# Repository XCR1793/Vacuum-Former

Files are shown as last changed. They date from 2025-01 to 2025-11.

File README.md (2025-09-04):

# Vacuum Former
An affordable vacuum former capable of forming medium to large bucks and molds. The system must also be safe for anyone to use in both hardware and electronics (as this requires mains).

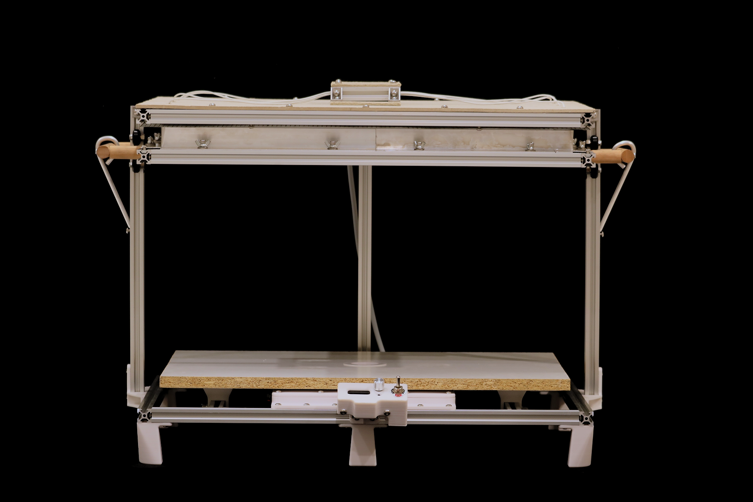
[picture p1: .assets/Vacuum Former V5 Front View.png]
Project_Image


## Features
* Hybrid Frame - Rigid aluminium combined with cheap cement fiber boards results in a fireproof frame.
* RCBO - Short, fault and overcurrent protection.
* SSR - PWM based temperature control.

## [Hardware](/Hardware/README.md)
The frame is designed to be collapsible so it is easily stored. The heater box, material frame and base plattern uses the same 440mm x 640mm aluminium 2020 frames which makes it easy to
fabricate and assemble. All components that get close to the heatsource is fireproof and areas that are not subject to heat are 3D printed to both save cost and time to construct.

## [Embedded](/Embedded/README.md)
Although dangerous, many safety features were implemented to reduce the risk of injury. This includes breakers and rcbos to detect shorts, faults and if the user accidentally touches the
live wires. All electronics are rated to and beyond what is required to run the system of 240VAC at 20A, this does mean however, that the user must have a port which can supply 15A and
beyond if you want to run the heater box. The average house hold outlet should provide 10A at 240VAC, however if your in the Americas you'll use 110VAC. This means in both senarios,
you will have to find a high current compatible port or else you will trip a breaker. If you dont have one, then you must remove 2 of the heating elements as each of them uses 1KW. This 
will however reduce the total amount of heat you can provided and may not be able to rais the temperature enough to heat difficult to form materials such as polycarbonate which requires 
around 240C to form properly.

## Roadmap
* Milestones: Hardware Assembly Complete
* Milestones: Electrical Wiring
* Milestones: Electrical Box
* Milestones: Controller Box
* Work In Progress: Datasheet
* Planned: Assembly Instructions

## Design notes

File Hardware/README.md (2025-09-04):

# Hardware

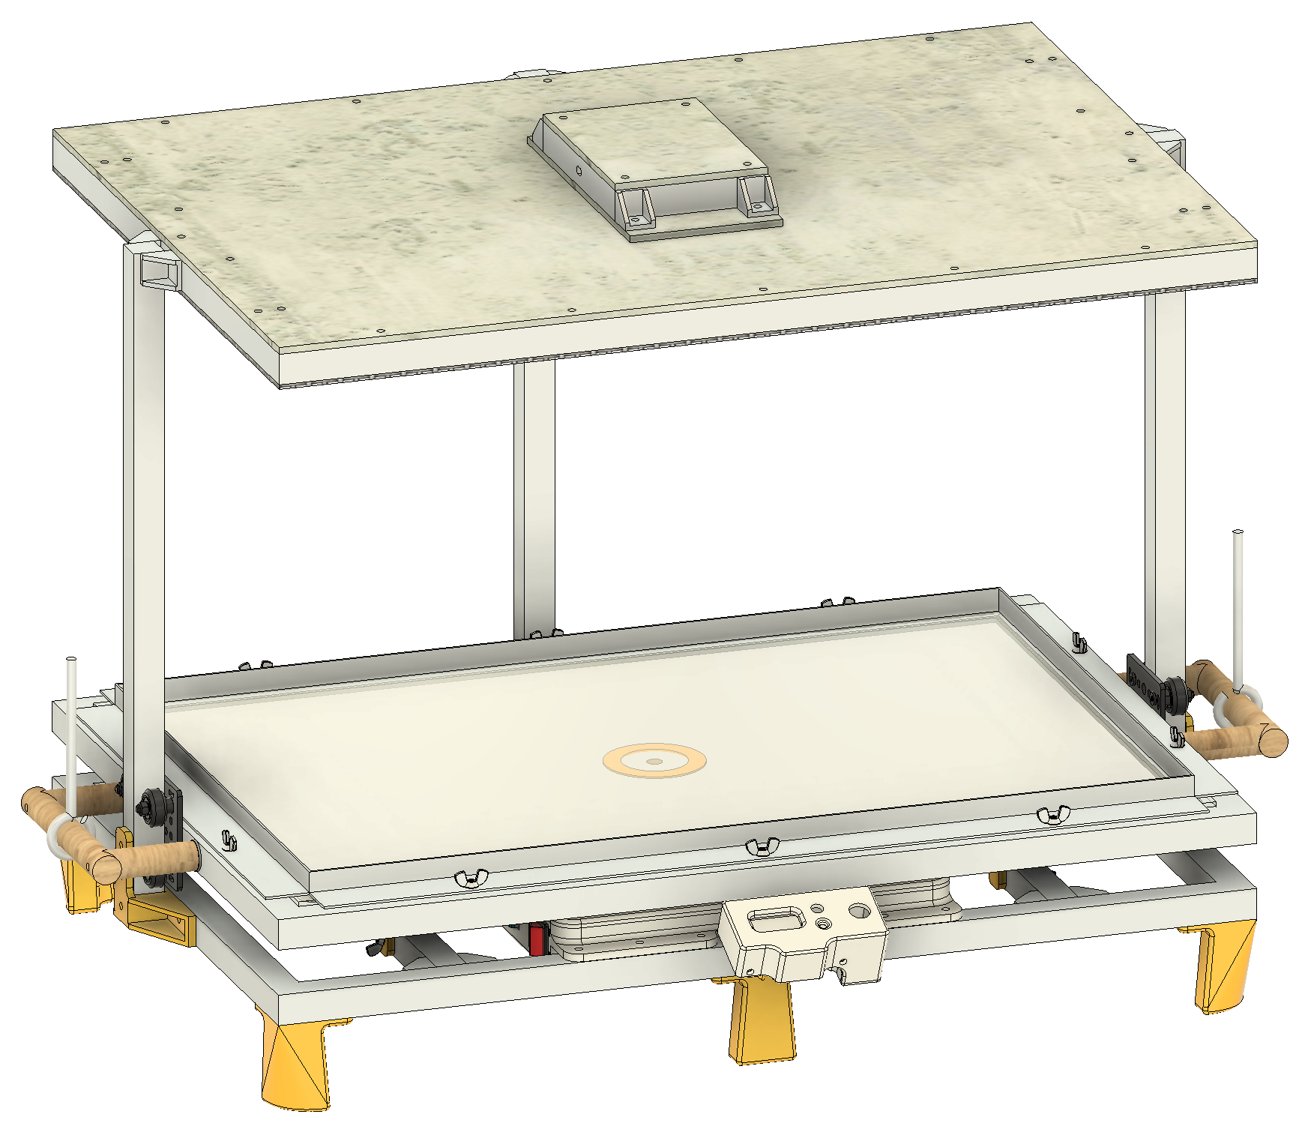
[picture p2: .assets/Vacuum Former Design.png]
Hardware_Capabilities


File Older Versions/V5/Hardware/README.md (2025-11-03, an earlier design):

# Hardware

Hardware_Capabilities

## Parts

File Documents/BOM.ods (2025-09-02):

Heater
Components | Size (mm) | Quantity
Aluminium Extrusion (2020) | 440 | 2
Aluminium Extrusion (2020) | 600 | 2
Aluminium Right Angle | 20 x 20 x 460 | 2
Metal Mesh | 440 x 640 | 1
Cement Fibre Board | 440 x 640 | 3
M5 Bolt | 10 | 18
M5 Bolt | 20 | 16
M5 T Nut | N/A | 30
Carbon Fibre Quartz Heater | 520 x 12 | 4
M5 Washer | N/A | 16
Material Frame
Components | Size (mm) | Quantity
Aluminium Extrusion (2020) | 440 | 2
Aluminium Extrusion (2020) | 600 | 2
Aluminium Right Angle | 30 x 15 x 958 | 2
Aluminium Right Angle | 20 x 12 x 1000 | 2
M5 Fly Nut | N/A | 10
M5 Bolt | 10 | 14
M5 Bolt (Fly Nut Male Adaptor) | 10 | 10
Platen
Components | Size (mm) | Quantity
Aluminium Extrusion (2020) | 440 | 2
Aluminium Extrusion (2020) | 600 | 2
Aluminium Extrusion (2020) | 400 | 2
Corner Bracket | N/A | 4
M5 Fly Nut | N/A | 4
M5 T Nut | N/A | 22
M5 Bolt | 10 | 12
Overall
Components | Size (mm) | Quantity
Aluminium Extrusion (2020) | 440 | 3
Aluminium 2020 Gantry Slider | N/A | 2
Corner Bracket | N/A | 6
Wooden Dowel (19mm OD) | 259 | 2
M5 Bolt | 75 | 4
M5 Washer | N/A | 4
M10 Washer | N/A | 4
M5 Bolt | 10 | 39
M5 T Nut | N/A | 43
Aluminium Rod (6.3mm OD) | 200 | 2
Electronics
Components | Size (mm) | Quantity
IEC C20 Port (Mains In) | N/A | 1
Anderson Port (Emergency Stop Port) | N/A | 1
IEC C19 Port (Heater Out) | N/A | 1
IEC C20 to Cables (Heater Adapter) | N/A | 1
Anderson to Cables (PWR Adapter) | N/A | 1
IEC C16 (Vacuum Pump Port) | N/A | 1
5V 2A PSU | 39 x 30 x 70 | 1
SSR (Heater, DC Controlled) | N/A | 1
SSR (Pump, DC Controlled) | N/A | 1
RCBO (20A) | N/A | 1
PWM Pulse Generator | N/A | 1
DPDT Switch (ON-Off-ON) | N/A | 1
Power Switch | N/A | 1
TOTAL Cost List |  | Total Cost: | $481.80 | AUD
Components | Size (mm) | Quantity | Cost (Total) | Link
Aluminium Extrusion (2020) | 1500 | 6 | $160.52 | Makerstore (https://www.makerstore.com.au/product/v-slot-20-x-20mm/?attribute_pa_length=1500mm)
Aluminium Right Angle | 20 x 20 x 1000 | 1 | $10.05 | Bunnings (https://www.bunnings.com.au/metal-mate-20-x-20-x-1-5mm-1m-aluminium-equal-angle-silver-1m_p1067865)
Aluminium Right Angle | 20 x 12 x 1000 | 2 | $16.32 | Bunnings (https://www.bunnings.com.au/metal-mate-20-x-12-x-1-4mm-1m-aluminium-unequal-angle-silver_p1067823)
Aluminium Right Angle | 30 x 15 x 1000 | 2 | $22.10 | Bunnings (https://www.bunnings.com.au/metal-mate-30-x-30-x-1-5mm-1m-silver-aluminium-angle-silver-1m_p1130510)
M5 Bolt | 10 | 83 | $14.77 | Aliexpress (https://www.aliexpress.com/item/1005007661689652.html?)
M5 T Nut | N/A | 115 | $17.62 | Aliexpress (https://www.aliexpress.com/item/1005007383347166.html?)
M5 Bolt | 20 | 16 | $12.71 | Aliexpress (https://www.aliexpress.com/item/32894530938.html?)
M5 Bolt | 75 | 4 | $2.05 | Bunnings (https://www.bunnings.com.au/pinnacle-m5-x-75mm-zinc-plated-round-head-bolts-and-nuts-4-pack_p0247271)
Carbon Fibre Quartz Heater | 520 x 12 | 4 | $51.37 | Aliexpress (https://www.aliexpress.com/item/1005007168603613.html?)
Aluminium Rod (6.3mm OD) | 1000 | 1 | $3.17 | Bunnings (https://www.bunnings.com.au/metal-mate-6-3mm-x-1m-aluminium-solid-rod-6-3mm_p1130541)
M5 Fly Nut | N/A | 14 | $6.61 | Aliexpress (https://www.aliexpress.com/item/1005006072038223.html?)
M5 Bolt (Fly Nut Male Adaptor) | 14mm | 14 | $9.13 | Aliexpress (https://www.aliexpress.com/item/32810872544.html?)
Cement Fibre Board | 440 x 640 | 3 | $12.55 | Bunnings (https://www.bunnings.com.au/james-hardie-hardieflex-2400-x-450-x-4-5mm-eaves-1-08m-_p0714491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)
Aluminium 2020 Gantry Slider | N/A | 2 | $10.99 | Aliexpress (https://www.aliexpress.com/item/1005006683869048.html?)
Metal Mesh | 440 x 640 | 1 | $14.99 | Bunnings (https://www.bunnings.com.au/rapidmesh-600-x-900-x-0-6mm-6-5-x-6-5-silver-wire-mesh-panel_p0203641)
Corner Bracket | N/A | 10 | $7.03 | Aliexpress (https://www.aliexpress.com/item/1005008248112282.html?)
Wooden Dowel (19mm OD) | 518 | 1 | $11.50 | Bunnings (https://www.bunnings.com.au/porta-19-x-19mm-1-2m-clear-pine-dowel_p8493988)
M10 Washer | N/A | 4 | $1.12 | Bunnings (https://www.bunnings.com.au/zenith-m10-hot-dip-galvanised-flat-round-washers_p2442070)
M5 Washer | N/A | 20 | $2.47 | Aliexpress (https://www.aliexpress.com/item/4000174460068.html?)
IEC C20 & C19 | N/A | 1 | $9.86 | Aliexpress (https://www.aliexpress.com/item/10000045738141.html?)
IEC C20 to Cables | N/A | 1 | $7.98 | Aliexpress (https://www.aliexpress.com/item/1005006996912471.html?)
IEC C16 (Vacuum Pump Port) | N/A | 1 | $5.93 | Aliexpress (https://www.aliexpress.com/item/1005005914216268.html?)
5V 2A PSU | 39 x 30 x 70 | 1 | $7.69 | Aliexpress (https://www.aliexpress.com/item/1005005552969433.html?)
SSR (DC Controlled AC) | N/A | 2 | $15.26 | Aliexpress (https://www.aliexpress.com/item/1005005837105164.html?)
RCBO (20A) | N/A | 1 | $41.29 | Bunnings (https://www.bunnings.com.au/deta-residual-circuit-breaker-with-overload-protection-20ah_p0131971)
PWM Pulse Generator | N/A | 1 | $6.72 | Aliexpress (https://www.aliexpress.com/item/1005006717341304.html?)
DPDT Switch (ON-Off-ON) | N/A | 1 | $11.96 | Aliexpress (https://www.aliexpress.com/item/1005004411546037.html?)
Power Switch | N/A | 1 | $5.90 | Aliexpress (https://www.aliexpress.com/item/33041128258.html?)

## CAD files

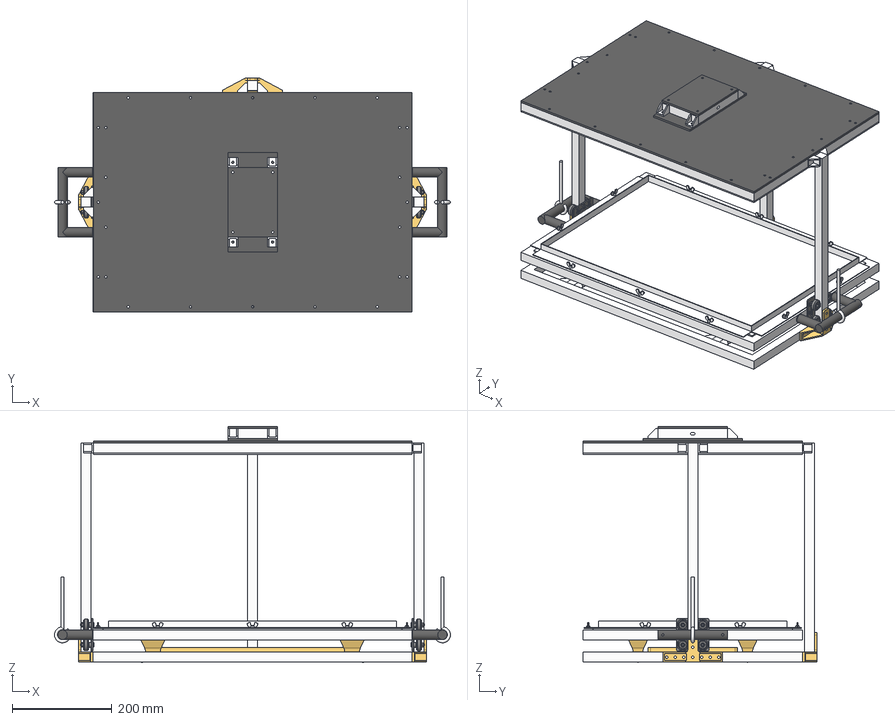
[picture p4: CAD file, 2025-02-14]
Hardware/Vacuum Former V5 Main.step
795.3 x 469.0 x 474.2 mm
V-Slot Gantry Plate 20mm x 2
Low Profile Screw M5 v1 x 8
Nylon Insert Lock Nut M5 x 8
Aluminum Spacer 6mm x 4
Eccentric Spacer 6mm v1 x 4
Ball Bearing 5 x 16 x 5 x 16
Precision Shim 8 x 5 x 1 x 8
Xtreme Solid V Wheel x 8
WING NUT M4 x 0.7mm Thread x 15
Carbon Fiber Quartz Heating Element (52cm) Ref x 4
Handles
Support Link R
Support Link L

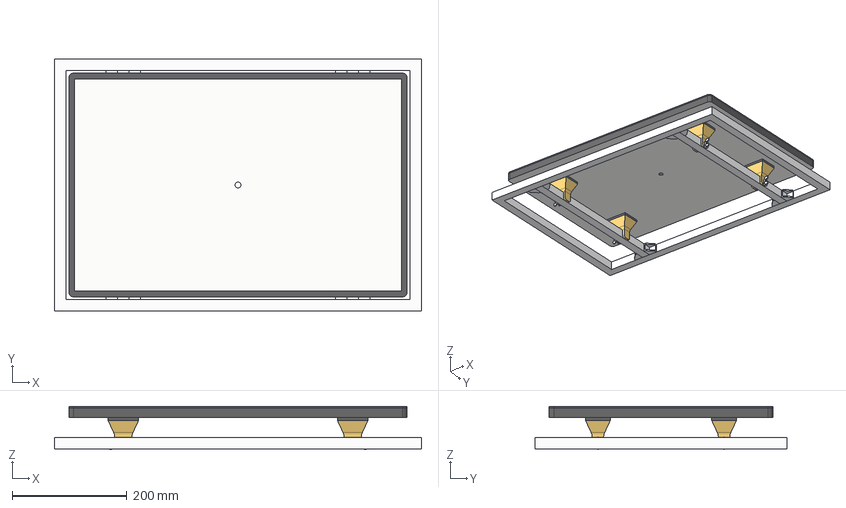
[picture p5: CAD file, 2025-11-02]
Hardware/Vacuum Former V5 Platen.step
640.0 x 440.0 x 75.2 mm
WING NUT M4 x 0.7mm Thread x 4

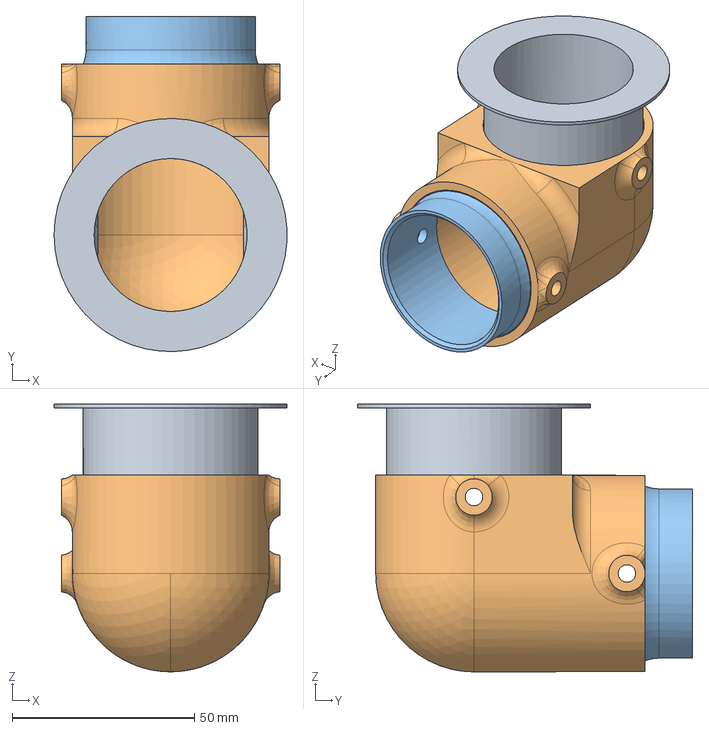
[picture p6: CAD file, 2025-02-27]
Hardware/Vacuum Former Platen Adapter V2.step
63.9 x 92.0 x 73.5 mm

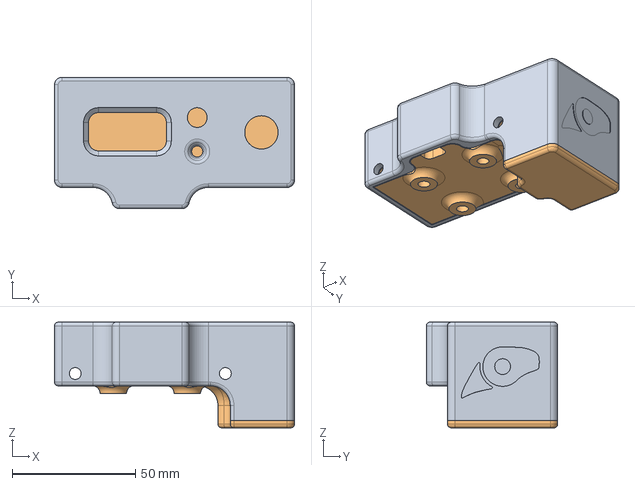
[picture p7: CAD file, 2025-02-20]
Hardware/Vacuum Former V5 Control Box.step
97.2 x 53.2 x 42.8 mm

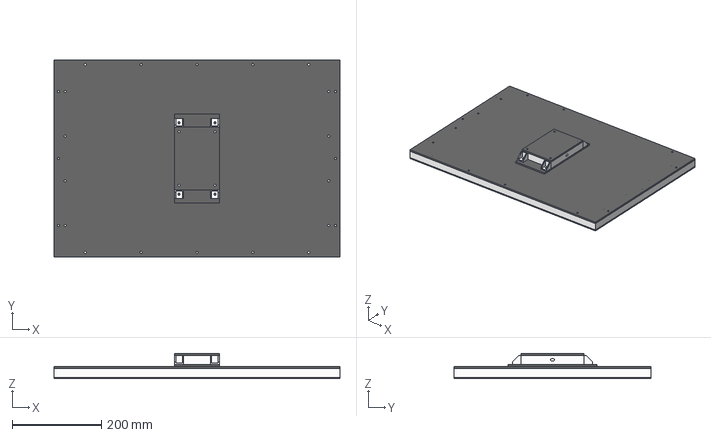
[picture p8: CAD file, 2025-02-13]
Hardware/Vacuum Former V5 Heater Box.step
640.0 x 440.0 x 56.5 mm
Carbon Fiber Quartz Heating Element (52cm) Ref x 4

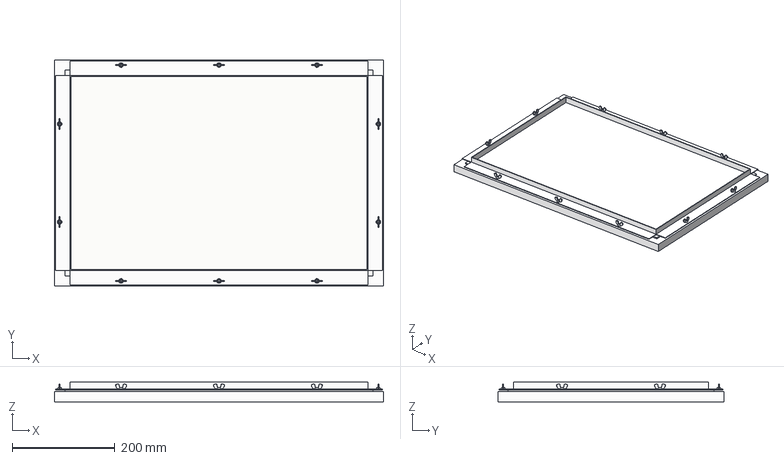
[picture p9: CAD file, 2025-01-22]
Hardware/Vacuum Former V5 Material Frame.step
640.0 x 440.0 x 38.0 mm
WING NUT M4 x 0.7mm Thread x 11

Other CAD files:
Hardware/Vacuum Former Platen Adapter V2.f3d
Hardware/Vacuum Former V5 Control Box.f3d
Hardware/Vacuum Former V5 Electrical Box.f3z
Hardware/Vacuum Former V5 Heater Box.f3z
Hardware/Vacuum Former V5 Main.f3z
Hardware/Vacuum Former V5 Material Frame.f3z
Hardware/Vacuum Former V5 Platen.f3z
Older Versions/V5/Hardware/Vacuum Former Platen Adapter V2.f3d
Older Versions/V5/Hardware/Vacuum Former V5 Control Box.f3d
Older Versions/V5/Hardware/Vacuum Former V5 Electrical Box.f3z
Older Versions/V5/Hardware/Vacuum Former V5 Heater Box.f3z
Older Versions/V5/Hardware/Vacuum Former V5 Main.f3z
Older Versions/V5/Hardware/Vacuum Former V5 Material Frame.f3z
Older Versions/V5/Hardware/Vacuum Former V5 Platen.f3z

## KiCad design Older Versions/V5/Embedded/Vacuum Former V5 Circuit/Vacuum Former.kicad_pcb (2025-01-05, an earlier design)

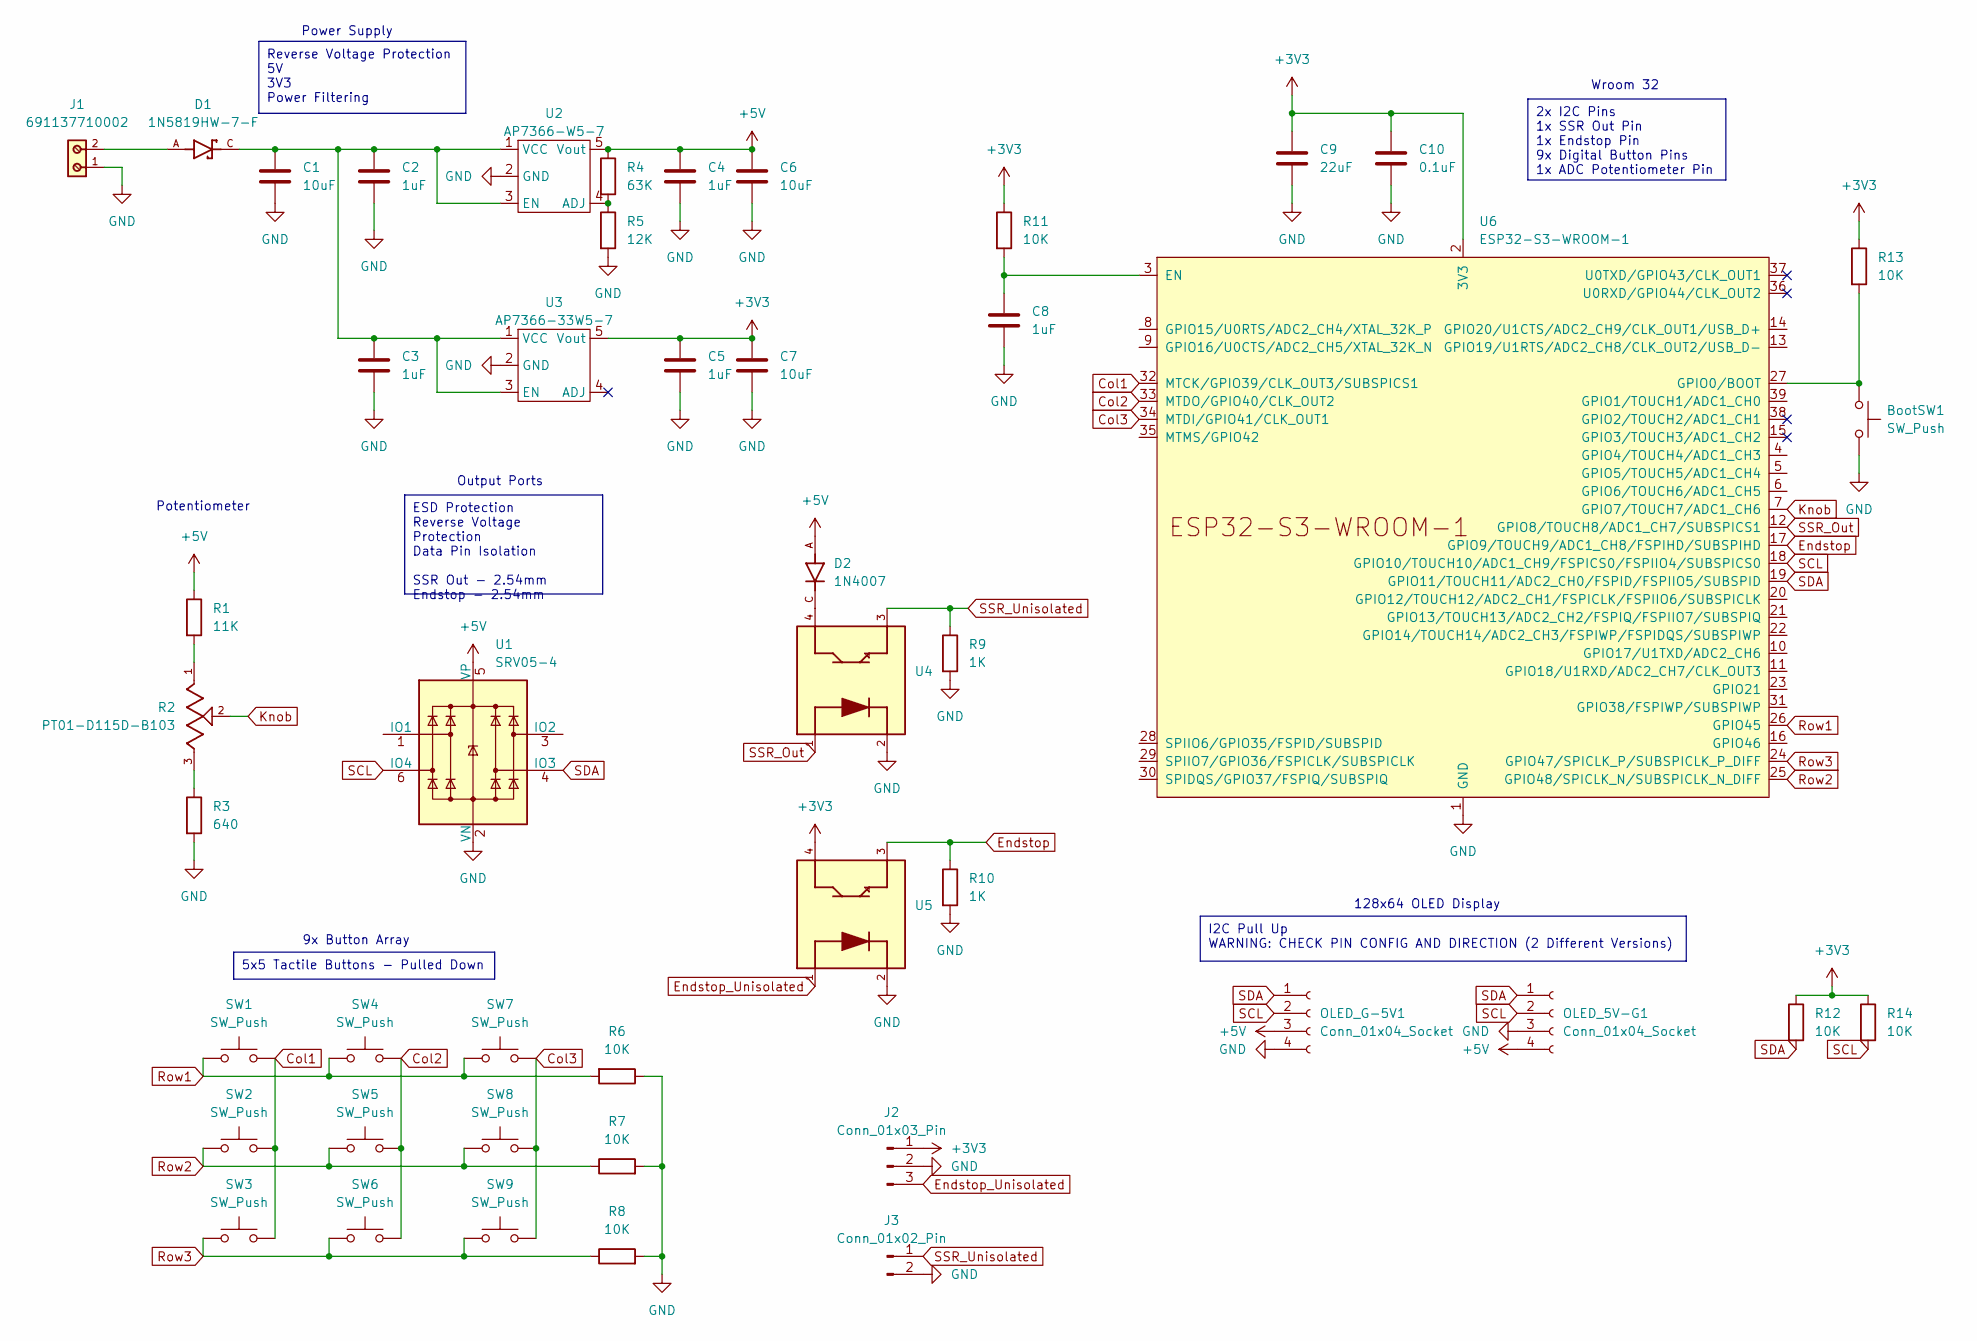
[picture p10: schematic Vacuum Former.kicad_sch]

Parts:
BootSW1: SW_Push; SW_PUSH_6mm
C1, C6, C7: 10uF; C_0603_1608Metric
C2, C3, C4, C5: 1uF; R_0603_1608Metric
C8: 1uF; C_0603_1608Metric
C9: 22uF; C_1206_3216Metric_Pad1.33x1.80mm_HandSolder
C10: 0.1uF; C_0603_1608Metric
D1: 1N5819HW-7-F; SOD3715X145N; PARTREV 18-2
D2: 1N4007; DIOAD1060W80L520D270; PARTREV G
J1: 691137710002; PART-NUMBER 691137710002
J2: Conn_01x03_Pin; PinHeader_1x03_P2.54mm_Vertical
J3: Conn_01x02_Pin; PinHeader_1x02_P2.54mm_Vertical
OLED_5V-G1: Conn_01x04_Socket; PinSocket_1x04_P2.54mm_Vertical
OLED_G-5V1: Conn_01x04_Socket; PinSocket_1x04_P2.54mm_Vertical
R1: 11K; R_0603_1608Metric
R2: PT01-D115D-B103; TRIM_PT01-D115D-B103; PARTREV 1.0
R3: 640; R_0603_1608Metric
R4: 63K; R_0603_1608Metric
R5: 12K; R_0603_1608Metric
R6, R7, R8, R12, R14: 10K; R_0603_1608Metric_Pad0.98x0.95mm_HandSolder
R9, R10: 1K; R_0603_1608Metric_Pad0.98x0.95mm_HandSolder
R11, R13: 10K; R_0603_1608Metric
SW1, SW2, SW3, SW4, SW5, SW6, SW7, SW8, SW9: SW_Push; SW_PUSH_6mm
U1: SRV05-4; SOT-23-6-routable
U2: AP7366-W5-7; AP7366
U3: AP7366-33W5-7; AP7366
U4, U5: SMD-PHOTOCOUPLER-5KV-LTV-816S_4P-4.6X6.5MM_; SMD4-2.54-4.6X6.5MM; MPN LTV-816S
U6: ESP32-S3-WROOM-1; ESP32-S3-WROOM-1U

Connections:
+3V3: C5.1, C7.1, C9.1, C10.1, J2.1, R11.1, R12.1, R13.1, R14.1, U3.5 (Vout), U5.4, U6.2 (3V3)
+5V: C4.1, C6.1, D2.A, OLED_5V-G1.4, OLED_G-5V1.3, R1.1, R4.1, U1.5 (VP), U2.5 (Vout)
Col1: SW1.2, SW2.2, SW3.2, U6.32 (MTCK/GPIO39/CLK_OUT3/SUBSPICS1)
Col2: SW4.2, SW5.2, SW6.2, U6.33 (MTDO/GPIO40/CLK_OUT2)
Col3: SW7.2, SW8.2, SW9.2, U6.34 (MTDI/GPIO41/CLK_OUT1)
Endstop: R10.1, U5.3, U6.17 (GPIO9/TOUCH9/ADC1_CH8/FSPIHD/SUBSPIHD)
Endstop_Unisolated: J2.3, U5.1
GND: BootSW1.2, C1.2, C2.2, C3.2, C4.2, C5.2, C6.2, C7.2, C8.2, C9.2, C10.2, J1.1, J2.2, J3.2, OLED_5V-G1.3, OLED_G-5V1.4, R3.2, R5.2, R6.1, R7.2, R8.2, R9.2, R10.2, U1.2 (VN), U2.2 (GND), U3.2 (GND), U4.2, U5.2, U6.1 (GND), U6.40 (GND), U6.41 (GND)
Knob: R2.2, U6.7 (GPIO7/TOUCH7/ADC1_CH6)
unnamed: D1.A, J1.2
unnamed: D2.C, U4.4
unnamed: R1.2, R2.1
unnamed: R2.3, R3.1
unnamed: R4.2, R5.1, U2.4 (ADJ)
unnamed: C1.1, C2.1, C3.1, D1.C, U2.1 (VCC), U2.3 (EN), U3.1 (VCC), U3.3 (EN)
unnamed: C8.1, R11.2, U6.3 (EN)
unnamed: BootSW1.1, R13.2, U6.27 (GPIO0/BOOT)
Row1: R6.2, SW1.1, SW4.1, SW7.1, U6.26 (GPIO45)
Row2: R7.1, SW2.1, SW5.1, SW8.1, U6.25 (GPIO48/SPICLK_N/SUBSPICLK_N_DIFF)
Row3: R8.1, SW3.1, SW6.1, SW9.1, U6.24 (GPIO47/SPICLK_P/SUBSPICLK_P_DIFF)
SCL: OLED_5V-G1.2, OLED_G-5V1.2, R14.2, U1.6 (IO4), U6.18 (GPIO10/TOUCH10/ADC1_CH9/FSPICS0/FSPIIO4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)
SDA: OLED_5V-G1.1, OLED_G-5V1.1, R12.2, U1.4 (IO3), U6.19 (GPIO11/TOUCH11/ADC2_CH0/FSPID/FSPIIO5/S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)
SSR_Out: U4.1, U6.12 (GPIO8/TOUCH8/ADC1_CH7/SUBSPICS1)
SSR_Unisolated: J3.1, R9.1, U4.3

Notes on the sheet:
ESD Protection Reverse Voltage Protection Data Pin Isolation SSR Out - 2.54mm Endstop - 2.54mm
Reverse Voltage Protection 5V 3V3 Power Filtering
2x I2C Pins 1x SSR Out Pin 1x Endstop Pin 9x Digital Button Pins 1x ADC Potentiometer Pin
5x5 Tactile Buttons - Pulled Down
I2C Pull Up WARNING: CHECK PIN CONFIG AND DIRECTION (2 Different Versions)
Wroom 32
Output Ports
128x64 OLED Display
9x Button Array
Potentiometer
Power Supply

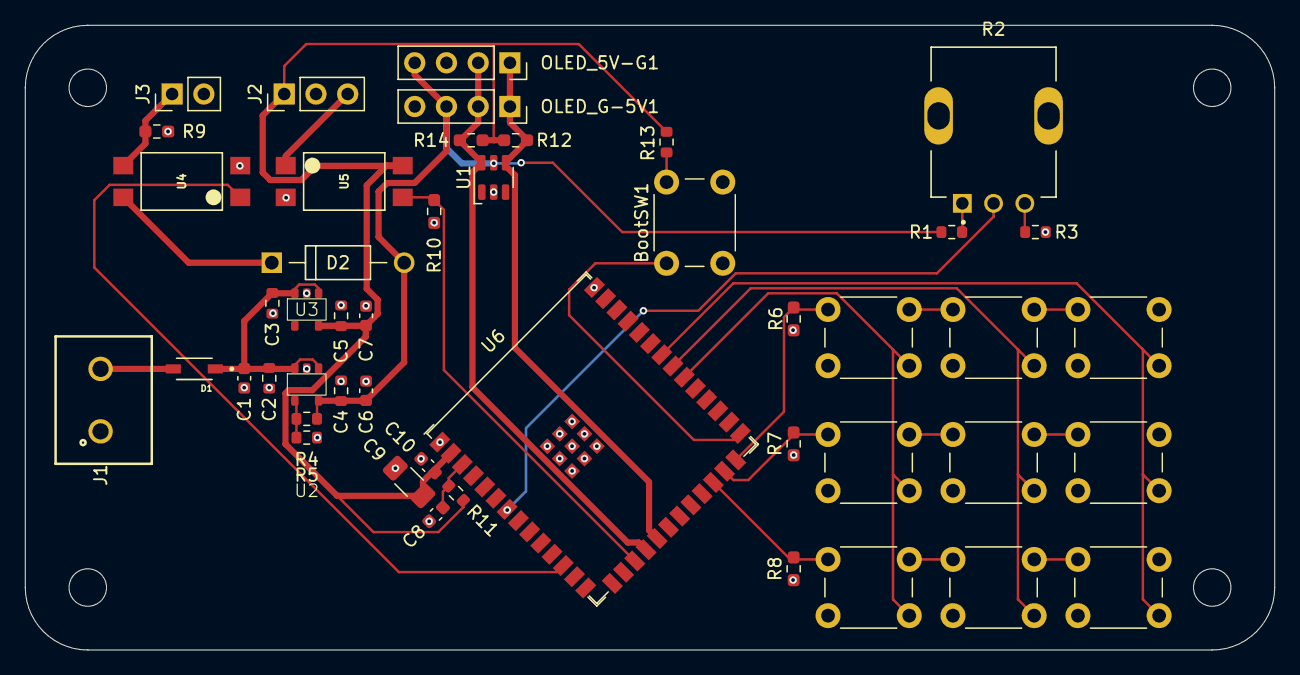
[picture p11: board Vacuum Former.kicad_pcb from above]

Board: 2 copper layers, 100.0 x 50.0 mm, 47 parts (0 on the bottom side), 24 nets.

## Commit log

2025-01-05 Migrated personal project files into public domain
    [Project.kicad_pcb, Project.kicad_sch, Vacuum Former.kicad_pcb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]
2025-01-05 Added Vertical Slider & Heater Box Ideation
2025-01-06 Ideation for Material Clamp
2025-01-07 Worked out material clamping
2025-01-08 Added Flat T Brackets for Added Rigidity
2025-01-09 Added Material Frame CAD
    [Vacuum Former V5 v1.step]
2025-01-10 More CAD Progress (Completed Heater Box)
2025-01-11 Added More CAD
2025-01-18 Modified Electrical Circuit
2025-01-22 Added Heater Box CAD
    [Vacuum Former V5 Heater Box.f3z, Vacuum Former V5 Heater Box.step, Vacuum Former V5 v1.step]
2025-01-22 Added Plattern CAD
    [Vacuum Former V5 Plattern.f3z, Vacuum Former V5 Plattern.step]
2025-01-22 Added Main Assembly CAD
    [Vacuum Former V5 Main.f3z, Vacuum Former V5 Main.step]
2025-01-25 Added Vacuum Former Handles
    [Vacuum Former V5 Main.f3z, Vacuum Former V5 Main.step]
2025-01-25 Added Vacuum Former Retainer Pin
    [Vacuum Former V5 Main.f3z, Vacuum Former V5 Main.step]
2025-01-26 Added BOM & Updated CAD
    [Spreadsheet.ods, Vacuum Former V5 Heater Box.f3z, Vacuum Former V5 Heater Box.step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]
2025-01-26 Added Total Lengths
    [Spreadsheet.ods]
2025-01-26 Added Extrusion & Right Angle
    [Spreadsheet.ods]
2025-01-26 Added Frame Bill of Materials
    [Spreadsheet.ods]
2025-01-26 Completed BOM (Verification Required before Order)
    [Spreadsheet.ods]
2025-01-27 Updated BOM before Ordering
    [Spreadsheet.ods]
2025-02-08 Updated Pricing
    [Spreadsheet.ods]
2025-02-12 Modified Spreadsheet to reflect IRL Build
    [Spreadsheet.ods]
2025-02-13 Optimised Heater Box for Ease of Assembly
    [Vacuum Former V5 Heater Box.f3z, Vacuum Former V5 Heater Box.step, Vacuum Former V5 Main.f3z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]
2025-02-13 Added Tolerances to Vertical Beam Mounts
    [Vacuum Former V5 Main.f3z, Vacuum Former V5 Main.step]
2025-02-14 Added Tolerances to Platern Supports
    [Vacuum Former V5 Main.f3z, Vacuum Former V5 Main.step, Vacuum Former V5 Platen.f3z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]
2025-02-17 Removed Placeholder Electronics Box
    [Vacuum Former V5 Platen.f3z, Vacuum Former V5 Platen.step]
2025-02-18 Added Correct Port Holes
2025-02-18 Added Controller Cable Hole
2025-02-19 Added Control Box & Modified Port Dimensions & Added Mounting Holes
    [Vacuum Former V5 Control Box.f3d, Vacuum Former V5 Control Box.step]
2025-02-20 Modified Box Dimensions to Fit PCB Better
    [Vacuum Former V5 Control Box.f3d, Vacuum Former V5 Control Box.step]
2025-02-22 Added Control Box Mount
2025-02-23 Modified electrical diagram to match real assembly
2025-02-26 Added Bolt Tolerances
    [Vacuum Former V5 Electrical Box.f3z, Vacuum Former V5 Main.f3z]
2025-02-27 Added Vacuum Platen Adapter
    [Vacuum Former Platen Adapter V2.f3d, Vacuum Former Platen Adapter V2.step]
2025-02-28 Modified Platen for IRL Wood Thickness
    [Vacuum Former V5 Platen.f3z, Vacuum Former V5 Platen.step]
2025-02-28 Added Legs
    [Vacuum Former V5 Main.f3z]
2025-03-08 Modified Electrical Box to Build Accurate Models
    [Vacuum Former V5 Electrical Box.f3z, Vacuum Former V5 Main.f3z]
2025-09-02 Modified File to BOM & Modified links (shortened)
    [BOM.ods, Spreadsheet.ods]
2025-09-04 Added Current vacuum former design
2025-10-31 Modified 3D Printed guide rail mounts
    [Vacuum Former V5 Main.f3z]
2025-11-02 Modified Platen supports to have easy mounting holes
    [Vacuum Former V5 Main.f3z, Vacuum Former V5 Platen.f3z, Vacuum Former V5 Platen.step]
2025-11-03 Modified File structure to have V5 in V5 folder in preparation for V5.1
    [BOM.ods, Vacuum Former Platen Adapter V2.f3d, Vacuum Former Platen Adapter V2.step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]
